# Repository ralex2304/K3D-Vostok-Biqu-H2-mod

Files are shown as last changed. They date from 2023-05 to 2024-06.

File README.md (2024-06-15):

# K3D Vostok Biqu H2 mod

Мод для Востока под установку голов с экструдерами Biqu H2, а также балкой оси X из алюминиевого квадратного профиля. Обдув двумя 5015 вентиляторомаи или удалённый обдув под CPAP трубку 15 мм. Очистители сопел для двухэкструдерной печати.

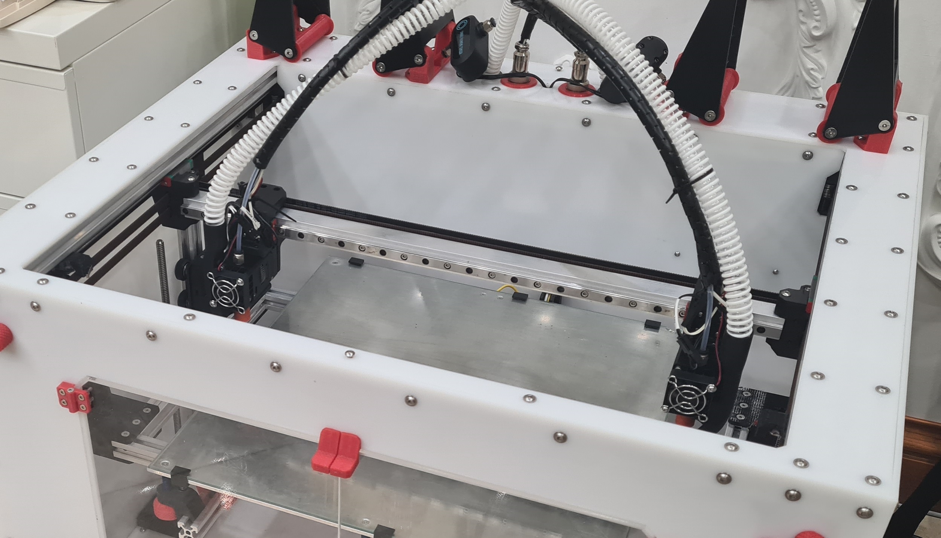
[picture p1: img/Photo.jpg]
Фото


### Плюсы
* Biqu H2 (возможность печатать очень мягкими TPU)
* Жёсткая балка из квадратного профиля
* Обдув 2х5015 или CPAP (Обдувы адаптированы для Volcano и CHC Pro, (v6 не тестировался))
* Очистители сопел

### Минусы
* Потеря около 35 мм области печати по Z
* Дороговизна H2

### Отличия от стока:
* Маунты голов (есть версия для MGN12H)
* Каретки Y:
  * Увеличена жёсткость
  * Прижим ремня передалан на алюминиевый
  * Крепление под квадратную балку X
* Маунты механических концевиков X и Y
* Маунты оптических концевиков Z
* Очистители сопел из силиконовых трубок (исключёно случайное прилипание выдавившегося для очистки пластика)

## Содержание репозитория:
* Сборка в формате .step
* Файлы для печати в формате .stl
* BOM (список необходимых деталей)
* [Указания](instructions/Printing%20recommendations.pdf) по ориентации деталей при печати и ручным поддержкам
* ~~Инструкция по сборке~~ (может быть когда-нибудь)

## 3D Сборка
* Модифицированные или новые детали в сборке выделены синим цветом
* Наименовавния новых деталей имеют вид M<версия мода>-<номера сборок и деталей>. В скобках указана стоковая заменённая деталь
* По умолчанию в модели показаны оба варианта обдувов, они накладываются друг на друга. Это не ошибка. В списке компонентов нужно скрыть неподходящий вариант

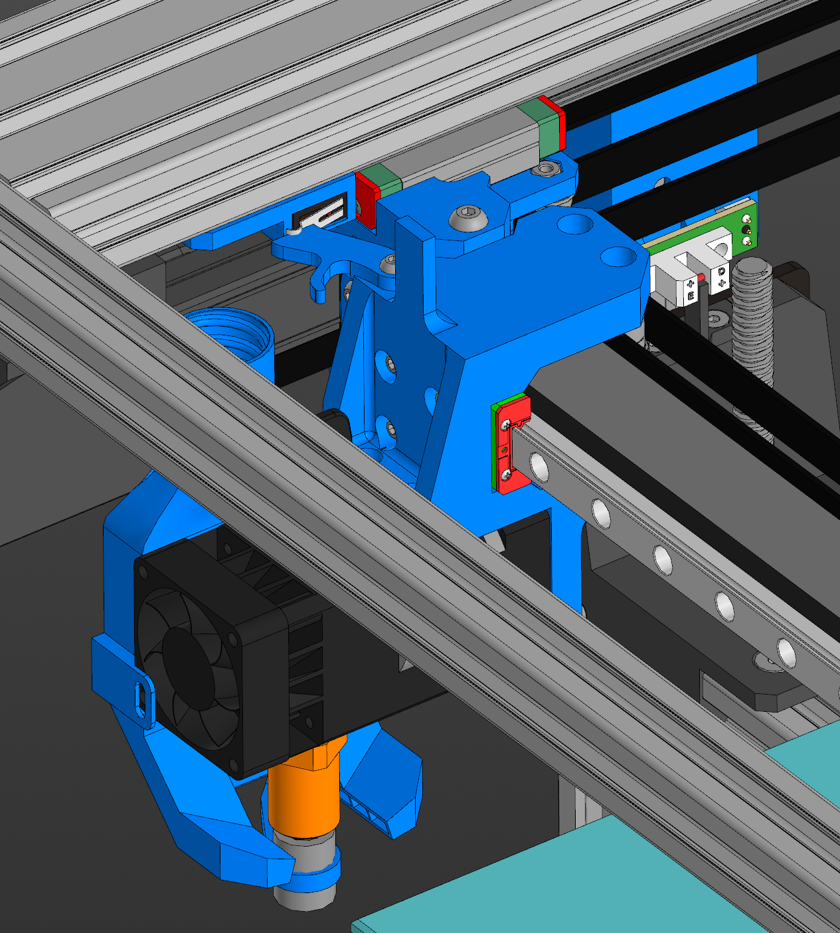
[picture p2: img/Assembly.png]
Изображение сборки


## Файлы для печати
Используйте те же рекомендации и настройки, что и в стоковом BOM. Во втором столбце указаны детали из стока, которые заменены новыми. Другие комментарии и количество деталей представлены в BOM

## BOM
Файл ods следует открывать в Libre Office (предпочтительно) или Google таблицах

## ~~Инструкция~~

# Благодарности
* Проект Восток (https://k3d.tech/vostok)
* Дмитрий Соркин (https://t.me/dsorkin) - автор проекта Восток, модель biqu h2 ([grabcad](https://grabcad.com/library/biqu-h2-dimensional-model-1))
* Юрий Кривенко (https://t.me/popingus) - основа маунтов балки и голов, модели обдувов
* .//Hack (https://t.me/DssHack) - маунты голов для MGN12H
* Alex Troiden - модель CHC Pro ([grabcad](https://grabcad.com/library/chc-pro-trianglelab-1))

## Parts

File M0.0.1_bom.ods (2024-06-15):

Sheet: Настройки
K3D Vostok Biqu H2 mod Здесь перечислены детали, изделия и крепёж, которые понадобятся вдобавок к тем, которые есть в BOM Востока. Из него не нужно будет приобретать все детали, относящиеся к печатным головам. То же и для печатных изделий (прочие замечания в комментариях к печатным изделиям). Из алюминиевого профиля не понадобится только балка оси X.
Параметр | Значение | Примечание
Экструдер
Количество экструдеров | 2 | 1 — обычный одиночный экструдер 2 — IDEX (две независимые печатающие головы)
Рельса оси X | MGN9 | MGN9 — в стоке установлена такая рельса MGN12 — для большей жёсткости можно установить рельсу MGN12 с каретками MGN12H
Обдув | CPAP | 2x5015 — обдув двумя вентиляторами 5015 CPAP — удалённый обдув CPAP
Ось Z
Длина балки оси X | 520 мм | Из основного BOM лист «Профиль алюминиевый»
Печатные детали
Плотность филамента для несущих деталей | 1,08 г/см³ | Характеристики филамента, который будет использоваться для печати нагруженных деталей механики принтера (каретки, детали печатающей головы и т. д.). Рекомендуется использовать прочный, жесткий, термостойкий и хорошо спекающийся материал. Например: PP GF; PP GF30; PA12 GF30; PA6 GF30 и подобные. Плотность указывается в г/см³, цена в $/кг.
Стоимость филамента для несущих деталей | 2 700,00 ₽ | Стоимость килограмма филамента, из которого будут печататься основные несущие детали принтера
Плотность филамента для вспомогательных деталей | 1,28 г/см³ | Характеристики филамента, который будет использоваться для печати вспомогательных деталей (петли, держатели катушек и т. д.). Рекомендуется прочный, дешевый и легкий в печати филамент с термостойкостью от 70 градусов. Идеальным выбором будет PETG, но возможна замена. Плотность указывается в г/см³, цена в $/кг.
Стоимость филамента для вспомогательный деталей | 1 200,00 ₽ | Стоимость килограмма филамента, из которого будут печататься основные несущие детали принтера
Константы
Курс доллара Aliexpress | 90,00 ₽ | Используется для примерной корректировки стоимости деталей, покупаемых с Aliexpress
Вывод: Стоимость
Покупные изделия | 20 286,00 ₽ | Для всех товаров не учтена стоимость доставки
Стандартные изделия | 394,80 ₽ | Самые дешевые винты
Алюминиевый профиль | 114,40 ₽ | Цена профиля из Leroy Merlin, стенка 1.5 мм (не рекомендуется)
Печатные детали | 826,83 ₽ | Без учёта вспомогательных структур
Итого стоимость | 21 622,03 ₽

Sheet: Покупные изделия
На данном листе производится расчёт количества нестандартных деталей Ссылки указаны на проверенные товары с хорошим качеством. Ссылки на часть товаров являются аффилиативными (Дмитрий Соркин). Покупая по ним вы поддерживаете проект.
Наименование | Удельная стоимость | Единиц | Общая стоимость | Ссылки | Альт. Ссылка | Примечание
Экструдер
Подающий механизм
Biqu H2 | 6 885,00 ₽ | 2 | 13 770,00 ₽ | AE (https://aliexpress.ru/item/1005002033057577.html)
Трубка очиститель сопла 1 м | 270,00 ₽ | 1 | 270,00 ₽ | AE (https://aliexpress.ru/item/1005004538286083.html?sku_id=12000029522279203) |  | Силиконовая трубка для очистки сопла в простое, ID 8 mm x 12 mm OD. Понадобится всего лишь 40 мм.
Система охлаждения | #ССЫЛ!
Вентилятор 5015 12-24в | 684,90 ₽ | 0 | 0,00 ₽ | AE (http://alli.pub/6fdf5h) |  | Вентилятор должен обязательно поддерживать ШИМ, иначе не будет возможности регулировать охлаждение
Вентилятор CPAP 24 вольта | 4 725,00 ₽ | 1 | 4 725,00 ₽ | AE (https://aliexpress.ru/item/10000048395481.html?sku_id=20000000115318794) |  | Вентилятор для удалённого обдува
Трубка CPAP 1,9 м | 1 350,00 ₽ | 1 | 1 350,00 ₽ | AE (https://aliexpress.ru/item/1005003620619783.html) |  | Трубка для удалённого обдува. Длину требуется проверить. Для области печати 400х350 и 2 голов 1,9 м трубки хватило впритык
Ось Y | #ССЫЛ!
Прижим ремня для кареток оси Y | 85,50 ₽ | 2 | 171,00 ₽ | AE (https://aliexpress.ru/item/32530843808.html) | RU (https://zona-3d.ru/catalog/mekhanika/zubchatye_remni/fiksatory_i_natyazhiteli_dlya_remney/fiksator-remnya-gt2-40-9)
Итого: |  |  | 20 286,00 ₽

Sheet: Стандартные изделия
 |  |  |  |  |  |  |  | Наименование сборки | K3D VOSTOK | XY portal | X axis | Y axis carriage | Biqu H2 print head |  | X axis mechanical endstop | Y axis mechanical endstop
 |  |  |  |  |  |  |  | Ед. | 1 | 1 | 1 | 2 | 2 | 2 | 2 | 2
Наименование | Стандарт | Резьба | Цена/ед. | Кол-во | Цена всего | Ссылки | Ссылка
Винт с полукруглой головкой и шестигранным углублением под ключ | ISO 7380-1 | М2х8 | 5,00 ₽ | 8 | 40,00 ₽ | krepcom (https://krepcom.ru/catalog/vinty-razdel/vint_2kh8_s_polukrugloy_golovkoy_i_vnutrennim_shestigrannikom_din_7380_prochnost_10_9.htm) | krep-shop (https://krep-shop.ru/katalog/bolty_i_vinty/iso_7380_1/2kh8-v-sh-p-kr-nerzh-a2-iso-7380/) |  |  |  |  |  |  |  | 2 | 2
 |  | М3х6 | 3,00 ₽ | 26 | 78,00 ₽ | krepcom (https://krepcom.ru/catalog/vinty-razdel/vint_3kh6_s_polukrugloy_golovkoy_i_vnutrennim_shestigrannikom_din_7380_nerzh_stal_a2.htm) | krep-shop (https://krep-shop.ru/katalog/bolty_i_vinty/iso_7380_1/3kh6_v_sh_p_kr_nerzh_a2_iso_7380/) |  |  |  |  | 4 | 9
 |  | M3x12 | 3,00 ₽ | 4 | 12,00 ₽ | krepcom (https://krepcom.ru/catalog/vinty-razdel/vint_3kh12_s_polukrugloy_golovkoy_i_vnutrennim_shestigrannikom_din_7380_nerzh_stal_a2.htm) | krep-shop (https://krep-shop.ru/katalog/bolty_i_vinty/iso_7380_1/3kh12_v_sh_p_kr_nerzh_a2_iso_7380/) |  |  |  |  |  |  | 2
 |  | М4х8 | 5,00 ₽ | 8 | 40,00 ₽ | krepcom (https://krepcom.ru/catalog/vinty-razdel/vint_4kh8_s_polukrugloy_golovkoy_i_vnutrennim_shestigrannikom_din_7380_nerzh_stal_a2.htm) | krep-shop (https://krep-shop.ru/katalog/bolty_i_vinty/iso_7380_1/4kh8_v_sh_p_kr_nerzh_a2_iso_7380/) |  |  |  |  |  |  |  | 2 | 2
 |  | М4х16 | 5,00 ₽ | 2 | 10,00 ₽ | krepcom (https://krepcom.ru/catalog/vinty-razdel/vint_4kh16_s_polukrugloy_golovkoy_i_vnutrennim_shestigrannikom_din_7380_nerzh_stal_a2.htm) | krep-shop (https://krep-shop.ru/katalog/bolty_i_vinty/iso_7380_1/4kh16_v_sh_p_kr_nerzh_a2_iso_7380/) |  |  |  |  | 1
 |  | М4х45 | 13,00 ₽ | 2 | 26,00 ₽ | krepcom (https://krepcom.ru/catalog/vinty-razdel/vint-polukrug-gol-vn-sh-iso-4-kh-45-din-7380-2-nerzh-a2.htm) | krep-shop (https://krep-shop.ru/katalog/bolty_i_vinty/iso_7380_1/4kh45_v_sh_p_kr_nerzh_a2_iso_7380/) |  |  |  | 2
Винт с потайной головкой и шестигранным углублением под ключ | DIN 7991 | М3х40 | 8,00 ₽ | 8 | 64,00 ₽ | krepcom (https://krepcom.ru/catalog/vinty-razdel/vint_potay_3kh40_stal_a2.htm) | krep-shop (https://krep-shop.ru/katalog/bolty_i_vinty/din_7991/3kh40_pot_v_sh_nerzh_a2_din_7991/) |  |  |  |  | 2 | 2
Винт с цилиндрической головкой и шестигранным углублением под ключ | DIN 912 | М3х25 | 5,00 ₽ | 8 | 40,00 ₽ | krepcom (https://krepcom.ru/catalog/bolty-razdel/bolt_vint_s_vnutrennim_shestigrannikom_i_tsilindricheskoy_golovkoy_din_912_3x25_nerzhaveyka_a2.htm) | krep-shop (https://krep-shop.ru/katalog/bolty_i_vinty/din_912/3kh25_v_sh_nerzh_a2_din_912/) |  |  |  |  |  | 4
Гайка шестигранная | DIN 934 | М3 | 2,00 ₽ | 8 | 16,00 ₽ | krepcom (https://krepcom.ru/catalog/gayki-razdel/gayka_sh_gr_m_3_DIN_934_ots.htm) | krep-shop (https://krep-shop.ru/katalog/gaiki/din_934/m3_nerzh_a_2_din_934/) |  |  |  |  | 2 | 2
 |  | М4 | 2,00 ₽ | 4 | 8,00 ₽ | krepcom (https://krepcom.ru/catalog/gayki-razdel/gayka_sh_gr_m_4_DIN_934_ots.htm) | krep-shop (https://krep-shop.ru/katalog/gaiki/din_934/m4_nerzh_a_2_din_934/) |  |  |  | 2 | 1
T-гайка с шариком |  | М4 | 7,60 ₽ | 8 | 60,80 ₽ |  | AE (https://alli.pub/6jzhxh) |  |  |  |  |  |  |  | 2 | 2
Итого: |  |  |  |  | 394,80 ₽

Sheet: Профиль алюминиевый
На данном листе производится расчёт параметров алюминиевого профиля. В качестве балки оси X используется алюминиевая труба квадратного сечения. Рекомендуется толщина стенки 2 мм. В таком случае рельсу оси X можно крепить на резьбу в самом профиле. В случае, если стенка меньше 2 мм, рекомендуется использовать гайки с фланцем. Профиль 1.5 мм гарантировано есть в Leroy Merlin. 2 мм нужно искать у себя в городе Leroy Merlin 1.5 мм (не рекомендуется) (https://leroymerlin.ru/product/profil-alyuminievyy-kvadratnyy-trubchatyy-20x20x15x1000-mm-12361030/)
Наименование детали | Тип профиля | Длина | Количество | Цена профиля [руб/мм] | Итого стоимость
Портал
Балка оси X | Квадратная труба 20х20х2 | 520 мм | 1 | 0,22 ₽ | 114,40 ₽
Итого: |  |  |  |  | 114,40 ₽

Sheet: Печатные изделия
На данном листе производится расчёт параметров печатных деталей Все детали, которые предполагается печатать из обычного, простого пластика, можно распечатать из продвинутого. Запечатка — это не процент заполнения! Этот параметр считается как объём пластика на деталь делить на объём детали и является очень приблизительным, нужен для общего представления о требовании к прочности только. То есть учитываются еще и периметры. Если запечатка 100%, то следует поставить 3-5 периметров (больше-лучше) и 100% заполнения. Если запечатка меньше 100%, то стоит поставить 5+ периметров и процент заполнения около 30. Рекомендации по ориентации моделей и поддержкам для печати находятся в pdf файле в папке «instructions»
Ось Z | Заменённая деталь из стока (не печатать) | Наименование | Объём | Пластик | Запечатка | Масса единицы | Количество | Итого стоимость | Поддержки | Комментарий
Печатные головы
M01-01-01-04-01-MGN9 | V08-01-01-04-01 | Biqu H2 mount | 46 166 мм³ | Продвинутый | 100,00% | 49,86 г | 2 | 269,24 ₽ | Ручные | Половина обычные, половина зеркальные
M01-01-01-04-01-MGN12 | V08-01-01-04-01 | Biqu H2 mount (DssHack) | 50 272 мм³ | Продвинутый | 100,00% | 54,29 г | 0 | 0,00 ₽ | Ручные | Половина обычные, половина зеркальные
M01-01-01-04-03 |  | X endstop trigger | 711 мм³ | Продвинутый | 100,00% | 0,77 г | 2 | 4,15 ₽ | Нет | Половина обычные, половина зеркальные
M01-01-01-04-02-01 |  | 5015 fan duct (Popingus) | 7 892 мм³ | Продвинутый | 100,00% | 8,52 г | 0 | 0,00 ₽ | Ручные | Для крепления нужно просверлить отверстия и нарезать резьбу M3 в корпусе biqu h2. Не зеркалить.
M01-01-01-04-02-03-L |  | Left CPAP duct | 16 496 мм³ | Продвинутый | 100,00% | 17,82 г | 1 | 48,10 ₽ | Ручные
M01-01-01-04-02-03-R |  | Right CPAP duct | 16 496 мм³ | Продвинутый | 100,00% | 17,82 г | 1 | 48,10 ₽ | Ручные
Портал
M01-01-01-01-01 | V08-01-01-01-01 | Y carriage base | 57 248 мм³ | Продвинутый | 100,00% | 61,83 г | 2 | 333,87 ₽ | Ручные | Половина обычные, половина зеркальные Деталь в папке с соответствующим названием. Требуется замерить толщину стенки трубы и выбрать файл, так как толщина стенки может не соответствовать заявленной
M01-01-01-05-02 | V08-01-01-05-02 | Tube cleaner holder | 9 982 мм³ | Продвинутый | 100,00% | 10,78 г | 2 | 58,22 ₽ | Нет | Половина обычные, половина зеркальные
M01-01-06-01 | V07-01-06-01 | X axis mechanical endstop mount | 3 183 мм³ | Простой | 100,00% | 4,07 г | 2 | 9,78 ₽ | Нет | Половина обычные, половина зеркальные
M01-01-07-01 | V08-01-07-01 | Y axis mechanical endstop mount | 2 311 мм³ | Простой | 100,00% | 2,96 г | 2 | 7,10 ₽ | Нет | Половина обычные, половина зеркальные
Ось Z
M01-03-05-01 | V07-03-05-01 | Optical endstop mount | 15 714 мм³ | Простой | 100,00% | 20,11 г | 2 | 48,27 ₽ | Нет | Половина обычные, половина зеркальные
Итого: |  |  |  |  |  |  |  | 826,83 ₽

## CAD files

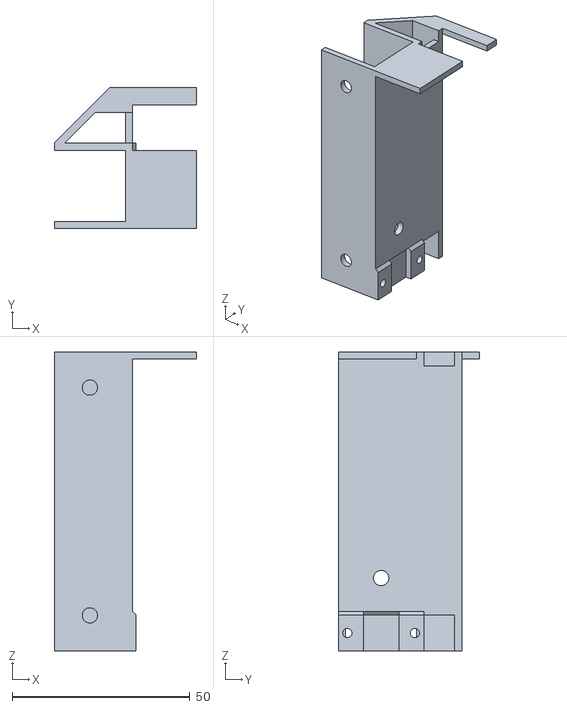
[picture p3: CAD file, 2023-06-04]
stl/M01-03-05-01 (V07-03-05-01) - Optical endstop mount.stl
40.0 x 39.6 x 84.0

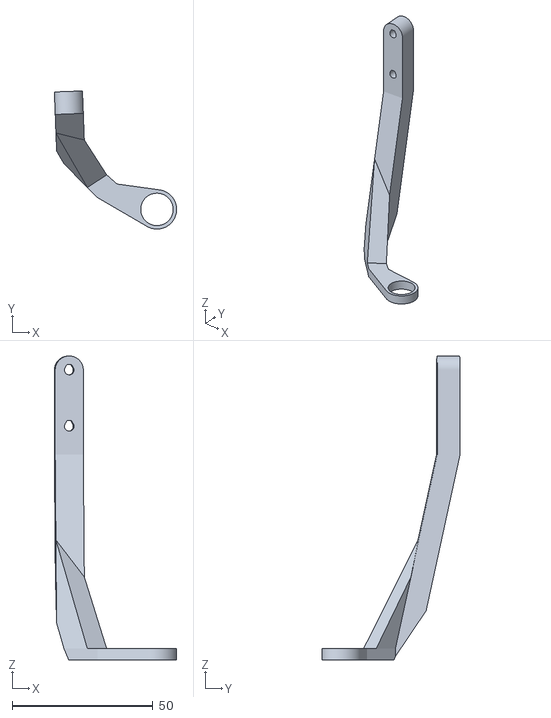
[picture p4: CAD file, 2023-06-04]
stl/M08-01-01-05-02 - Tube cleaner holder.stl
43.4 x 49.1 x 108.0

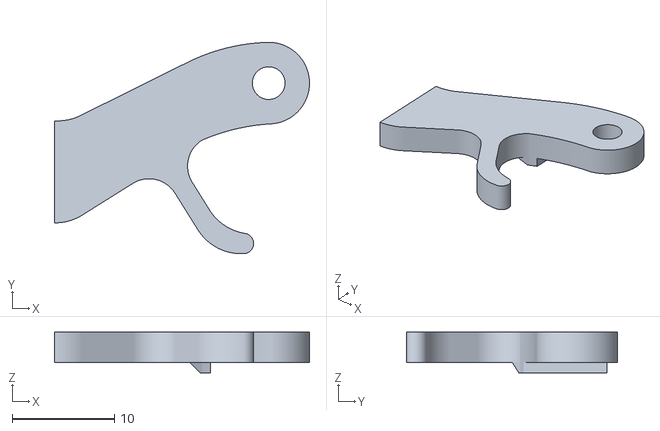
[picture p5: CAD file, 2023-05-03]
stl/M01-01-01-04-03 - X endstop trigger.stl
25.0 x 20.7 x 4.00

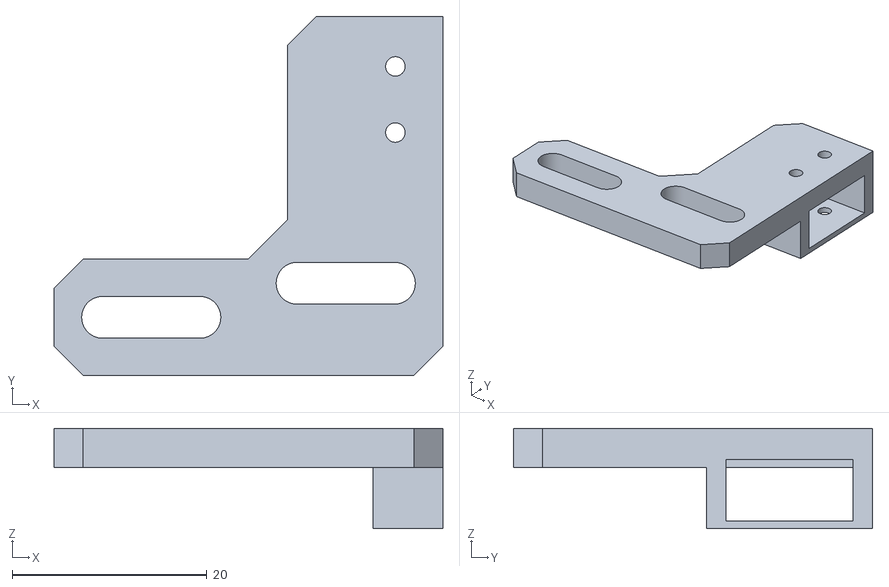
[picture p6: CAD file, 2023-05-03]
stl/M01-01-06-01 (V07-01-06-01) - X axis mechanical endstop mount.stl
40.0 x 37.0 x 10.3

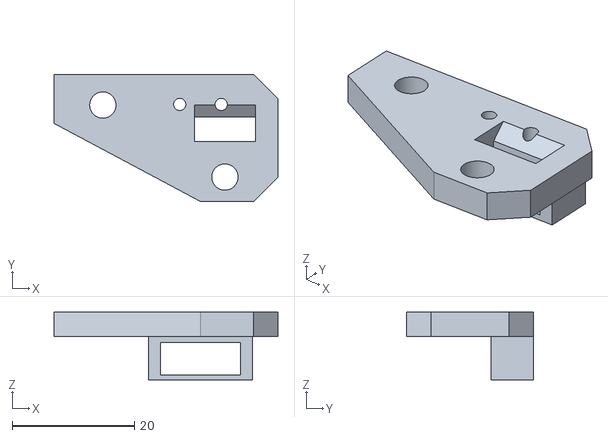
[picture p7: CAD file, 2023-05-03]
stl/M01-01-07-01 (V07-01-07-01) - Y axis mechanical endstop mount.stl
36.7 x 20.8 x 11.1

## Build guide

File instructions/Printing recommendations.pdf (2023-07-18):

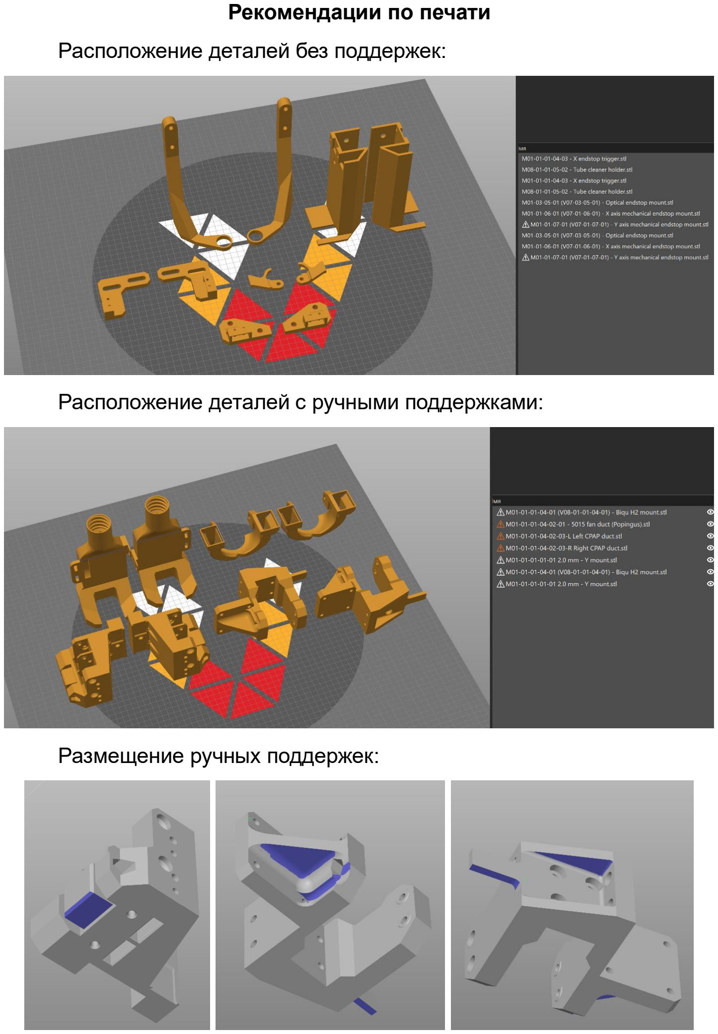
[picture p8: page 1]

Рекомендации по печати

Расположение деталей без поддержек:

Расположение деталей с ручными поддержками:

Размещение ручных поддержек:

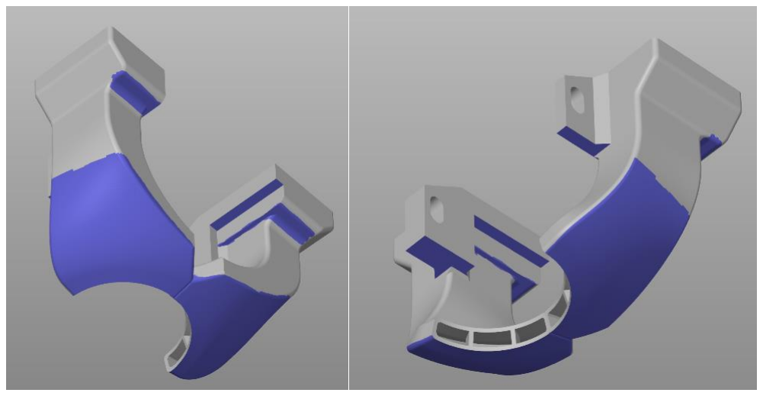
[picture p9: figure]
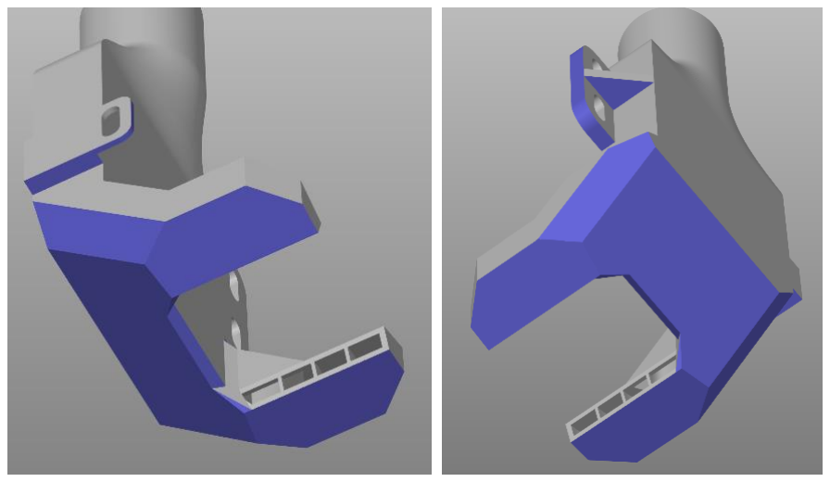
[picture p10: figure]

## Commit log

2023-05-16 Right cpap duct thread fix
2023-06-04 Tube holder and Z endstop holder fix
    [M01-03-05-01 (V07-03-05-01) - Optical endstop mount.stl, M08-01-01-05-02 - Tube cleaner holder.stl]
2023-06-05 Y mount cleaner holder holes fix
2023-06-11 H2 mount back screws fix
2023-07-18 CPAP two-sided ducts + printing recommendations
    [M0.0.1_bom.ods]
2024-06-15 Добавлен маунт головы для MGN12H
    [M0.0.1_bom.ods]
